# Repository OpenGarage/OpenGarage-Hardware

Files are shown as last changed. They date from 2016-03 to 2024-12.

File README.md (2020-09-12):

OpenGarage is a WiFi universal garage door opener based on the ESP8266 chip.

For details, visit [http://opengarage.io](http://opengarage.io)

This folder contains OpenGarage hardware design files, including:

* Schematic and Board files (EagleCAD)
* BOM, Pin assignments
* Enclosure design files
  - The original 3D design can be found at TinkerCad.com -> search for OpenGarage

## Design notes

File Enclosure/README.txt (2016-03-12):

The 3D printable version is available at:

TinkerCad.com

Search for name 'OpenGarage'.

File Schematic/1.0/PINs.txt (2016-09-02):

ESP8266-WROOM-2 PIN ASSIGNMENTS:

'spare' means the pin is available
for general purpose use and mapped
out on the PCB.

GPIO 0: BUTTON
GPIO 2: LED
GPIO 4: SDA (spare)
GPIO 5: SCL (spare)
GPIO12: SENSOR TRIGGER
GPIO13: BUZZER
GPIO14: SENSOR ECHO
GPIO15: RELAY
GPIO16: RESET (tied to reset to trigger hardware reset)
A0    : ANALOG PIN (spare)

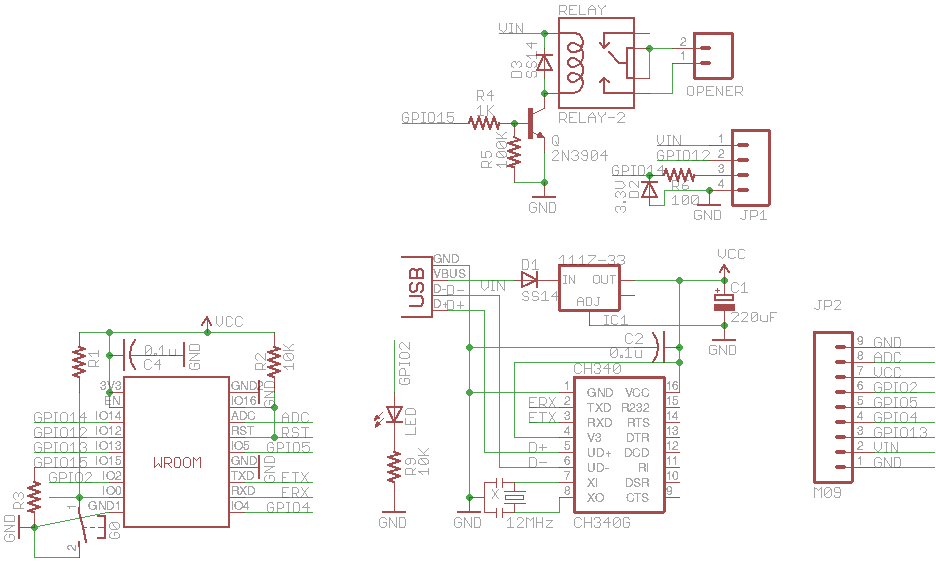
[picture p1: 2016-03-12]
Schematic/1.0/og1.0.png

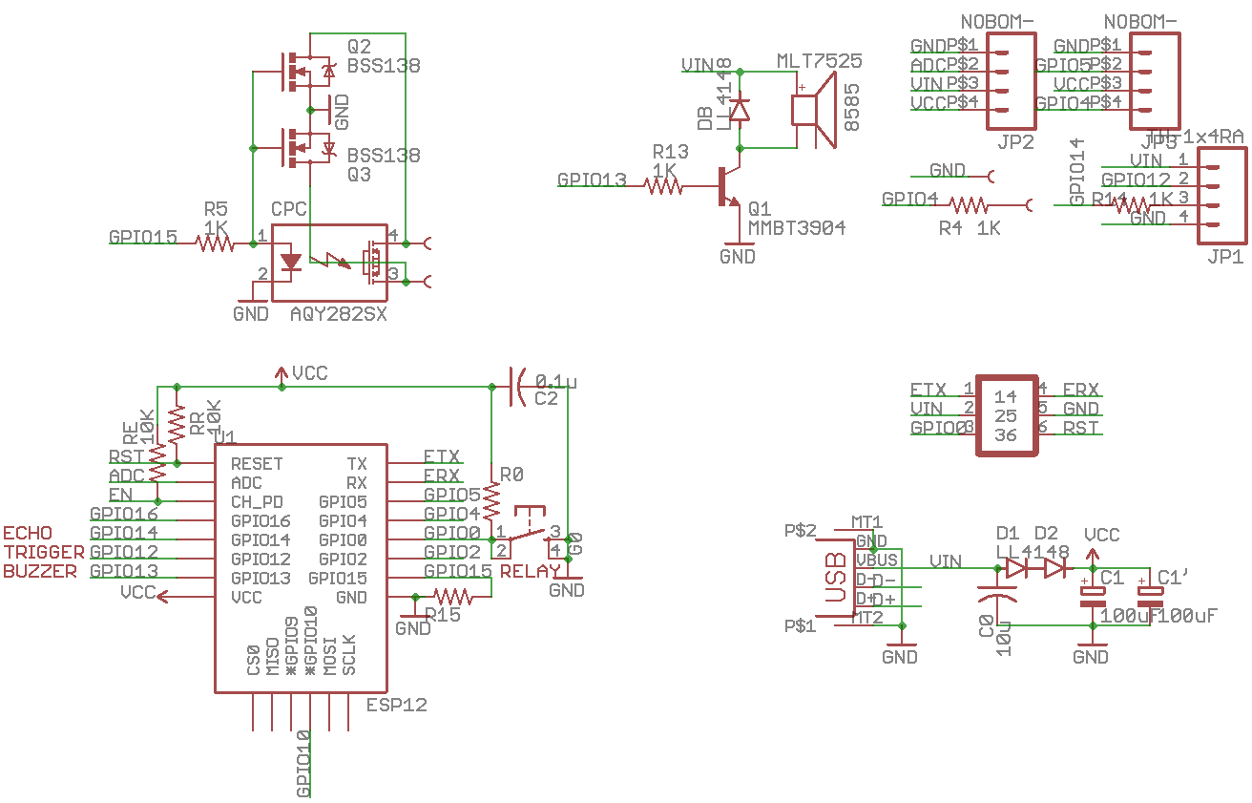
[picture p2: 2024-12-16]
Schematic/2.2/og22_schematic.png

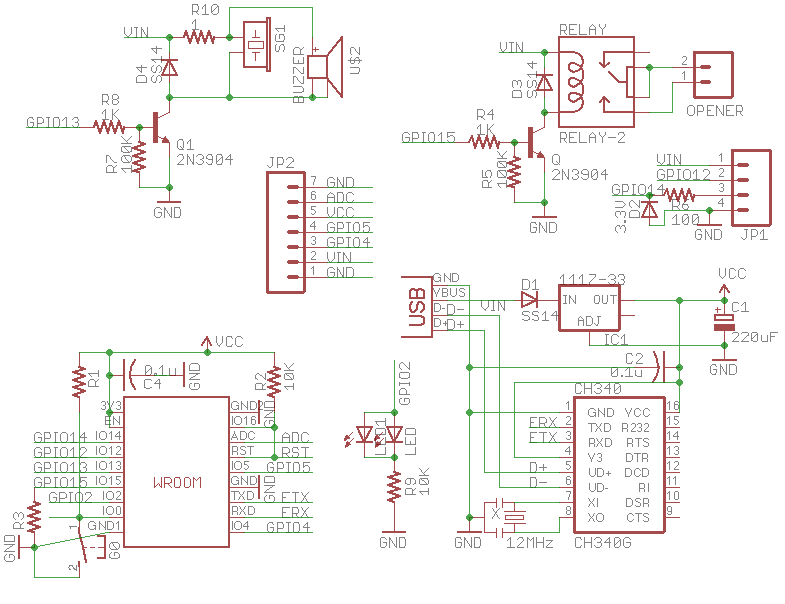
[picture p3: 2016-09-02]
Schematic/1.1/og1.1.png

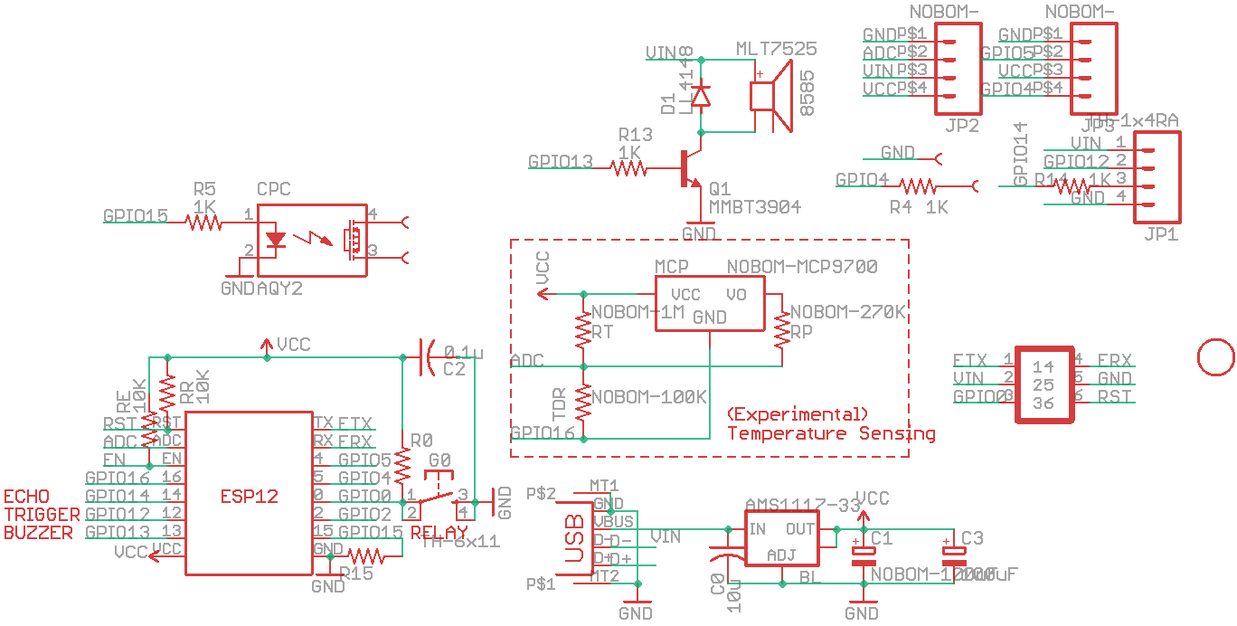
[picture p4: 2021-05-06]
Schematic/2.0/og20_rev2.png

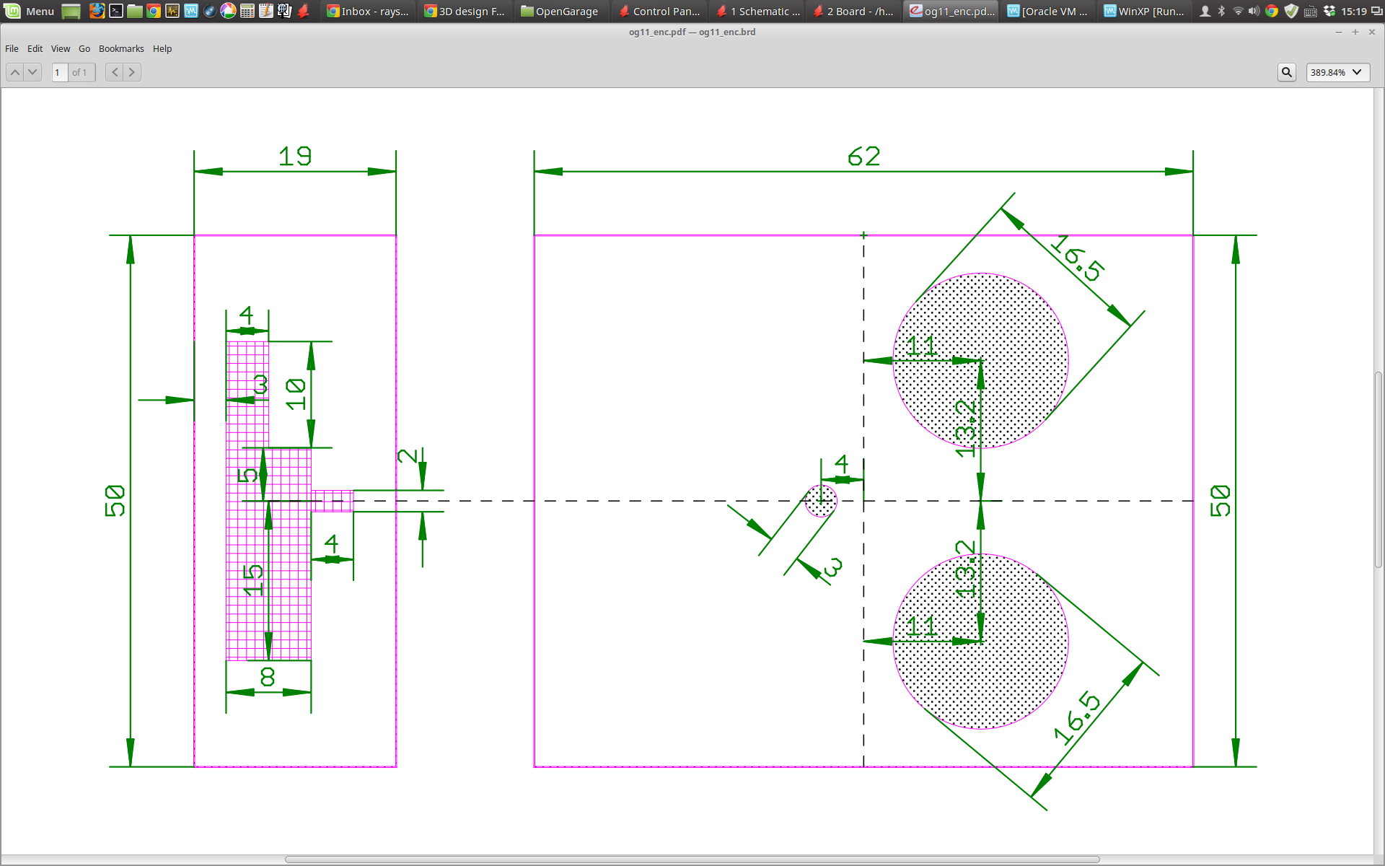
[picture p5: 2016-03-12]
Enclosure/pre-1.4/cutout.png

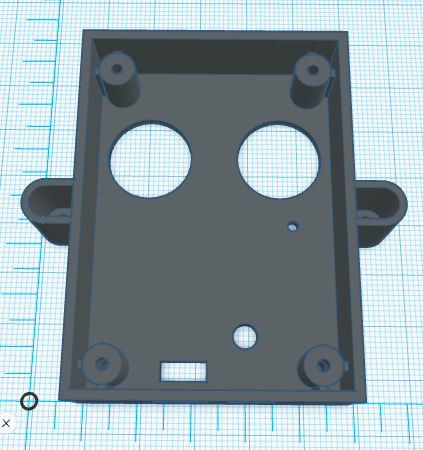
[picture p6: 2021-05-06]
Enclosure/1.4/OG1.4_ENC.png

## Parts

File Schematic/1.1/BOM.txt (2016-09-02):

Part List

Part   Value      Device                Package               Description                          

C1     220uF      CPOL-EUCT3528         CT3528                POLARIZED CAPACITOR, European symbol 
C2     0.1u       C-USC0603K            C0603K                CAPACITOR, American symbol           
C4     0.1u       C-USC0603K            C0603K                CAPACITOR, American symbol           
CH340  CH340G     CH340G                SO16                                                       
D1     SS14       DIODE-DO-214AC        DO-214AC              DIODE                                
D2     3.3V       DIODE-MINIMELF        MINIMELF              DIODE                                
D3     SS14       DIODE-DO-214AC        DO-214AC              DIODE                                
D4     SS14       DIODE-DO-214AC        DO-214AC              DIODE                                
ESP    WROOM02    WROOM02               WROOM                                                      
G0                31-XX                 B3F-31XX              OMRON SWITCH                         
IC1    1117-33    V_REG_LM1117SOT223    SOT223                Voltage Regulator LM1117             
JP1    ULTRASONIC HC-SR04               HC-SR04                          
LED               LEDLED3MM_ABBRV       LED3MM_ABBRV          LED                                  
LED1              LEDCHIPLED_0805       CHIPLED_0805          LED                                  
OPENER OPENER     M024MM-X              SCREWTERMINAL-4MM-2-X Header 2                             
Q      2N3904     TRANSISTOR_NPNSOT23-3 SOT23-3               Transistor NPN                       
Q1     2N3904     TRANSISTOR_NPNSOT23-3 SOT23-3               Transistor NPN                       
R1     10K        R-US_R0603            R0603                 RESISTOR, American symbol            
R2     10K        R-US_R0603            R0603                 RESISTOR, American symbol            
R3     10K        R-US_R0603            R0603                 RESISTOR, American symbol            
R4     1K         R-US_R0603            R0603                 RESISTOR, American symbol            
R5     100K       R-US_R0603            R0603                 RESISTOR, American symbol            
R6     100        R-US_R0603            R0603                 RESISTOR, American symbol            
R7     100K       R-US_R0603            R0603                 RESISTOR, American symbol            
R8     1K         R-US_R0603            R0603                 RESISTOR, American symbol            
R9     10K        R-US_R0603            R0603                 RESISTOR, American symbol            
R10    1          R-US_R0603            R0603                 RESISTOR, American symbol            
RELAY  RELAY-2    HK4100F-5VDC          HK4100F-5VDC                                            
SG1               BUZZERPTH             BUZZER-12MM           Buzzer 12mm                          
U$2    BUZZER     BUZZER                SMT-8585-BUZZER                                            
X      12MHz      RESONATORSMD          RESONATOR-SMD         Resonator                            
X3     USB-MICROB USB-MICROB            USB-MICROB            USB Connectors

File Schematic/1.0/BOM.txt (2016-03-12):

Partlist

Part     Value          Device                Package               

C1       220uF          CPOL-EUCT3528         CT3528                
C2       0.1u           C-USC0603K            C0603K                
C4       0.1u           C-USC0603K            C0603K                
CH340    CH340G         CH340G                SO16                  
D1       SS14           DIODE-DO-214AC        DO-214AC              
D2       3.3V Zener     DIODE-MINIMELF        MINIMELF              
D3       SS14           DIODE-DO-214AC        DO-214AC              
ESP      WROOM02        WROOM02               WROOM                 
G0                      31-XX                 B3F-31XX              
IC1      1117-33        LM1117-ee             SOT223                
JP1      ULTRASONIC     DISTANCE SENSOR       1X04_SONICSENSOR      
LED                     LEDLED3MM_ABBRV       LED3MM_ABBRV          
OPENER   OPENER         M024MM-X              SCREWTERMINAL-4MM-2-X 
Q        2N3904         2N3902                SOT23-3               
R1       10K            R-US_R0603            R0603                 
R2       10K            R-US_R0603            R0603                 
R3       10K            R-US_R0603            R0603                 
R4       1K             R-US_R0603            R0603                 
R5       100K           R-US_R0603            R0603                 
R6       100            R-US_R0603            R0603                 
R9       10K            R-US_R0603            R0603                 
RELAY    RELAY-2        RELAY-2               RELAY-HK4100F-5VDC
X        12MHz          RESONATORSMD          RESONATOR-SMD         
X3       USB-MICROB     USB-MICROB            USB-MICROB

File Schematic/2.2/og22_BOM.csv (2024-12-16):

Name | Designator | Footprint | Quantity
0.1u | C2 | C0603K | 1
1K | R4,R5,R13,R14 | R0603 | 4
10K | R0,R15,RE,RR | R0603 | 4
10u | C0 | C0805K | 1
100uF | C1, C1' | PANASONIC_C | 2
BSS138 | Q2-3 | SOT23-3 | 2
ESP12 | U1 | ESP12E-SMD | 1
LL4148 | D1,D2,DB | MINIMELF | 3
MICROXNJ | X3 | USB-MICROB2 | 1
MLT7525 | 8585 | SMT-8585-BUZZER | 1
MMBT3904 | Q1 | SOT23-3 | 1
TH-1x4RA | JP1 | 1X04_SONICSENSOR_EXT2 | 1
TH-6x11 | G0 | EVQ-Q2 | 1

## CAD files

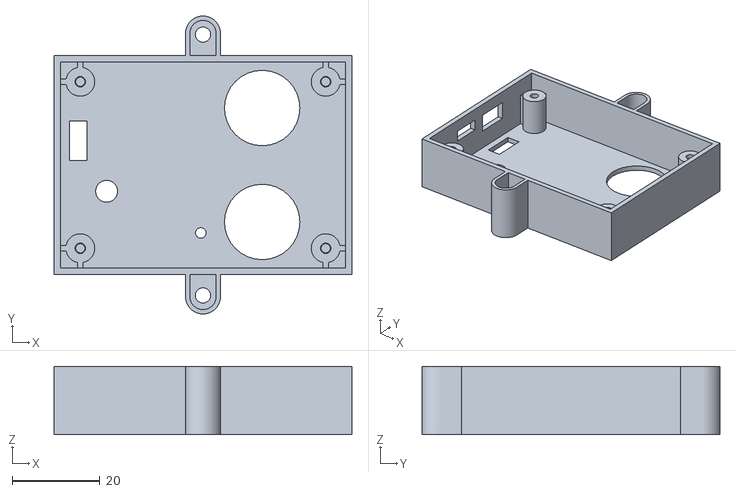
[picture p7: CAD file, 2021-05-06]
Enclosure/1.4/OpenGarage1.4_single.stl
68.0 x 68.0 x 15.6

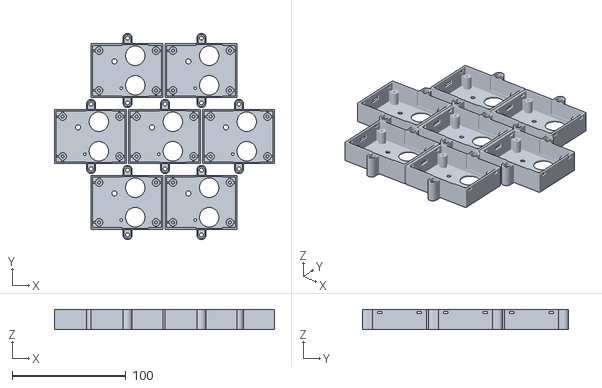
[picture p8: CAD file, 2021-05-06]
Enclosure/2.0/OG2.0ENC.stl
193.4 x 181.4 x 17.6

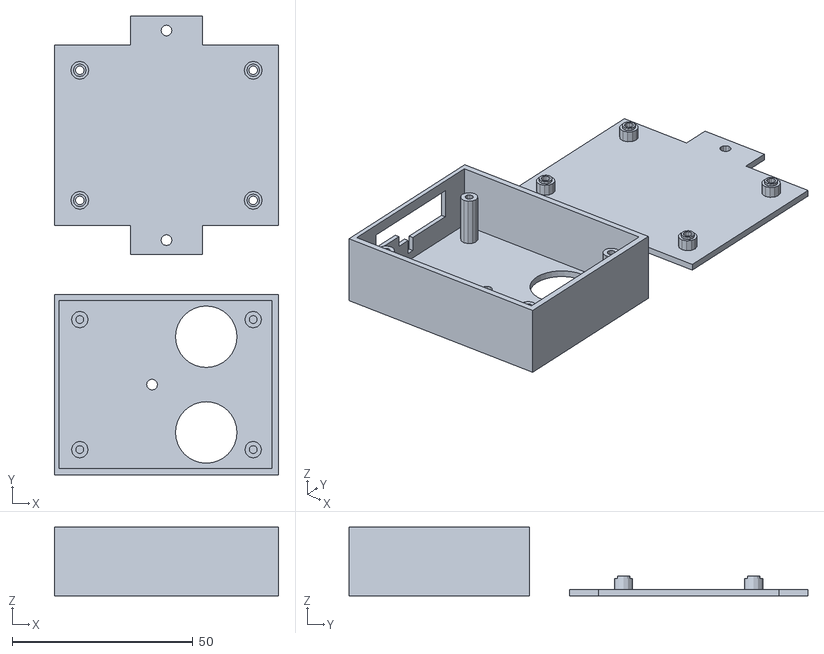
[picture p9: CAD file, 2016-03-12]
Enclosure/pre-1.4/enclosure_3d.obj
62.0 x 127.0 x 19.0

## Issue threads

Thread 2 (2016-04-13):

Value of R9

terrag42, 2016-04-13:
I noticed that in your schematic and in the BOM, R9 is specified as 10k Ohms. If I'm using a normal LED whose rated voltage is about 3.2V, I don't think it will be very bright, is this what you have found? Since the LED's voltage is coming from the ESP8266 (3.3 V), would it be OK for me to change the value of R9 to something like 220 ohms or even 47 ohms?

rayshobby, 2016-04-20:
Sorry, that's a typo. It should be something small (like 220ohm or 330ohm).

Closed 2016-04-20.

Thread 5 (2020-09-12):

Version 1.4 Open Source Hardware Version?

wiesl, 2020-09-12:
Hello,

Ordered 2x OpenGarage Hardware. Unfortunately this is Version V1.4 of OpenGarage Hardware.

Where can I find V1.4 of the Schematic and PCB Eagle files?

Thnx.

rayshobby, 2020-09-12:
I've just checked it in.

wiesl, 2020-09-13:
Thnx.

Closed 2020-09-12.

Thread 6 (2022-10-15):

What type is C3 on the 2.0 Hardware

Dreamoffice, 2022-10-15:
Hello

what type is the condensator C3?

rayshobby, 2022-10-24:
The BOM has each component's type and value:
https://github.com/OpenGarage/OpenGarage-Hardware/blob/master/Schematic/2.0/og20_rev2_BOM.csv

Closed 2022-10-24.

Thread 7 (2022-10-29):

missing part? buzzer not working

Dreamoffice, 2022-10-29:
Hello. i just assembled one Opengarage 2.0 but the buzzer is not working. how can i trouble shoot? this is my board. did i missed some parts except the ultra sonic sensor?

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

rayshobby, 2022-10-31:
Q1 (MMBT3904) on your board is missing.

Closed 2022-10-31.

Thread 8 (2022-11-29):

Feature request: control garage lights

danepowell, 2022-11-29:
Most garage doors include 120 V lights on the power head that automatically turn on when the garage opens, and can also be controlled by a switch on the opener.

It would be awesome to control these lights with OpenGarage. I'm guessing this would require a second relay, since the light button has its own control wire (green for old Genie models like mine).

rayshobby, 2022-11-29:
I've looked at this a while back. This highly depends on the garage door system. I have a LiftMaster (non-security+ 2.0), and I noticed its door button has a light control switch. It uses the same two wires for door control and light control. I took apart the door button panel, and found that the door control simply shorts the two wires (as expected), and the light control connects a 1uF capacitor across the two wires. Some online posts also documented this feature:
https://forum.arduino.cc/t/using-esp8266-arduino-and-2n2222-for-garage-door/472101
I've actually made a variant of OpenGarage that uses two solid state relays, the first one simply shorts the two wires, and the second one has a 1uF capacitor in series. This allows for controlling both the door and the light.

However, if a garage door system uses security+ 2.0, then it's a completely different story -- it uses rolling code so is not as simple as connecting a 1uF capacitor across the two wires. I am sure other brands would use yet different ways for light control. So I concluded it would be hard to design one circuit that handles all these different ways for light control.

danepowell, 2022-11-30:
Makes sense, thanks a lot for the context. I wonder if you could leave some open slots on the board for folks to insert their own relays or caps or daughter board to accommodate whatever system. Maybe that's overkill :shrug:

Closed 2023-11-16.

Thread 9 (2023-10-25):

Possible to use with LA400 Gate Opener?

TopBanana123, 2023-10-25:
I'm wondering if its possible to connect this up to an LA400 gate opener? Its a fairly recent model and also apparently has single button control on the circuit board

rayshobby, 2023-11-16:
If directly wiring OpenGarage to your door's button terminals doesn't work, then as long as you have a working button/remote, you can always solder two wires to the button/remote, and wire them to OpenGarage. That should always work.

Closed 2023-11-16.

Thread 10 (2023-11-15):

Enclosure not found on TinkerFiles

TopBanana123, 2023-11-15:
I have an issue with the OpenGarage enclosure in that it does not accept a standard USB cable because the USB Port is too recessed

I made the hole bigger and in the process cracked the case, and would like to print another. The GitHub page does to search for OpenGarage on TinkerHub, however I get no results

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

Is there an STL file I could get to print another?

HoECoder, 2023-11-16:
I found them here:
https://www.tinkercad.com/things/fSLeOxNVjwK-opengarage-enclosure

And here:
https://www.tinkercad.com/things/2qRHEHzTHSL-opengarage-enclosure-v2

Depending on your HW Version

rayshobby, 2023-11-16:
The 3D model in STL format is available in the Enclosure folder:
https://github.com/OpenGarage/OpenGarage-Hardware/tree/master/Enclosure

TopBanana123, 2023-11-16:
Perfect, thanks guys! Would be nice if the main page linked to the STL instead of asking you to search

Closed 2023-11-16.

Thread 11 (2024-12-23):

SSR dead for the second time

tofuSCHNITZEL, 2024-12-23:
Hi,
I have an OG Rev 2.0 and I just had to swap the SSR for the second time in around a year because it was completely fried and did not switch anymore...
maybe this is caused by the particular garagemotor I have but I was just wondering if you have some experience with dying solid state relays on the opengarage board...?

cheers

rayshobby, 2025-01-25:
This is likely due to your garage door system is presenting a high voltage to OpenGarage. The SSR can tolerate up to 60V. I've seen very occasionally some garage door systems that present 110V, which will definitely fry the SSR. Have you measured the voltage on the two wires of your garage door system? Almost all modern systems use 12VDC, which is well below the limit. If this continues to be a problem, you may want to use an electromechanical relay which can tolerate up to 220V.

tofuSCHNITZEL, 2025-01-25:
I admit I have not yet measured the "switching" wires because I assumed that they come pot-free from the garage motor pcb... but probably not ;) I have wired a "real" relay to the opengarage pcb and I don't expect any issues anymore ;) thanks!

Closed 2025-01-25.

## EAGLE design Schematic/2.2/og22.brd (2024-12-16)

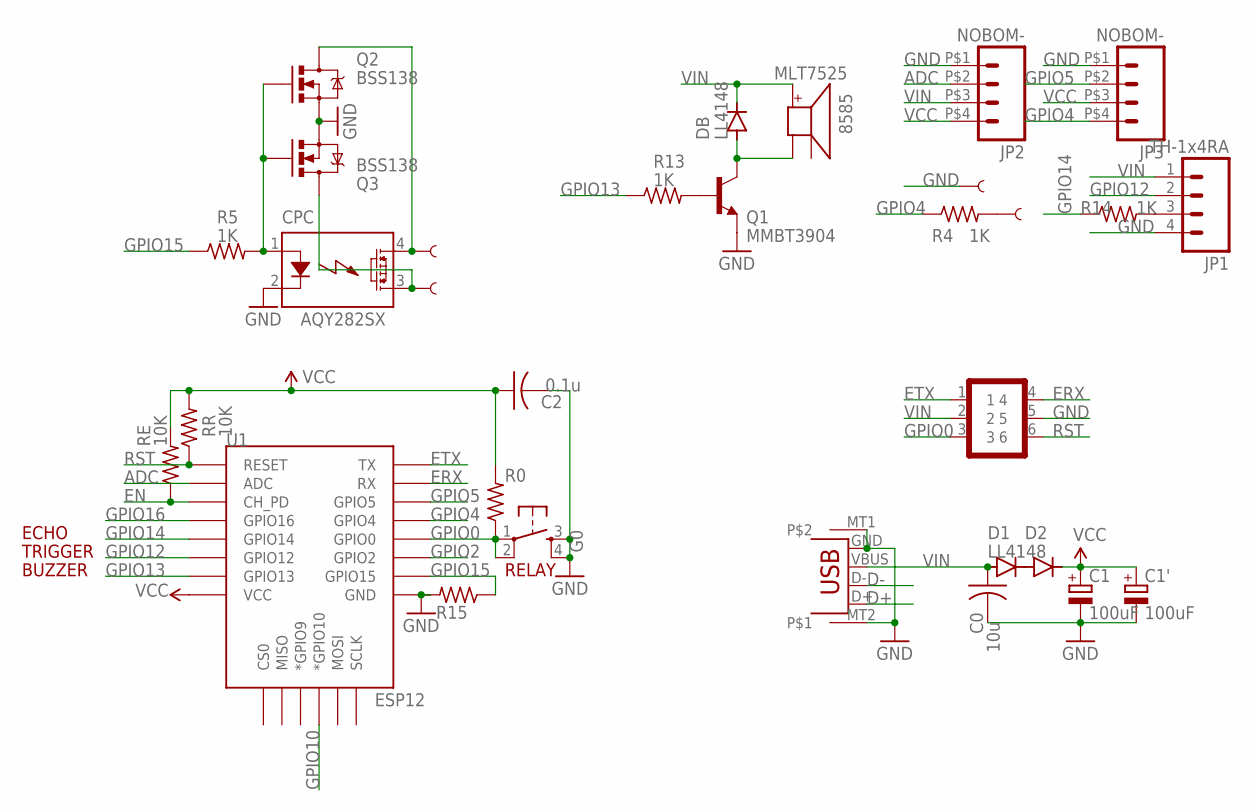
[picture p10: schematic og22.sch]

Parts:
8585: MLT7525; SMT-8585-BUZZER
C0: 10u; C0805K
C1, C1': 100uF; PANASONIC_C
C2: 0.1u; C0603K
CPC: AQY282SX; PHOTOMOS
D1, D2: LL4148; MINIMELF
DB: LL4148; MINIMELF
G0: TH-6x11; EVQ-Q2
JP1: TH-1x4RA; 1X04_SONICSENSOR_EXT2
JP2, JP3: NOBOM-; 1X04-2X2
Q1: MMBT3904; SOT23-3
Q2, Q3: BSS138; SOT23-3
R0, R15: 10K; R0603
R4, R5, R13, R14: 1K; R0603
RE: 10K; R0603
RR: 10K; R0603
U1: ESP12; ESP12E-SMD
U$1: NOBOM-GF2x3; GOLDFINGER_2X3
U$2, U$3, U$4, U$5: NOBOM-; PETAL-7MM-DOUBLE
X3: MICROXNJ; USB-MICROB2

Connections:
ADC: JP2.P$2 (2), U1.ADC
D+: X3.D+
D-: X3.D-
EN: RE.1, U1.CH_PD
ERX: U1.RXD0 (RX), U$1.4
ETX: U1.TXD0 (TX), U$1.1
GND: C0.2, C1.-, C1'.-, C2.2, CPC.2 (K), G0.3, G0.4, JP1.4, JP2.P$1 (1), JP3.P$1 (1), Q1.2 (E), Q2.2 (S), Q3.2 (S), R15.2, U1.GND, U$1.5, U$4.P$1, X3.GND, X3.MT1, X3.MT2
GPIO0: G0.1, G0.2, R0.1, U1.GPIO0, U$1.3
GPIO2: U1.GPIO2
GPIO4: JP3.P$4 (4), R4.1, U1.GPIO4
GPIO5: JP3.P$2 (2), U1.GPIO5
GPIO10: U1.GPIO10 (*GPIO10)
GPIO12: JP1.2, U1.GPIO12
GPIO13: R13.1, U1.GPIO13
GPIO14: R14.1, U1.GPIO14
GPIO15: R5.1, R15.1, U1.GPIO15
GPIO16: U1.GPIO16
unnamed: CPC.4 (DS1), Q2.3 (D), U$3.P$1
unnamed: CPC.3 (DS2), Q3.3 (D), U$2.P$1
unnamed: R4.2, U$5.P$1
unnamed: JP1.3, R14.2
unnamed: 8585.-, DB.A, Q1.3 (C)
unnamed: Q1.1 (B), R13.2
unnamed: CPC.1 (A), Q2.1 (G), Q3.1 (G), R5.2
unnamed: D1.C, D2.A
RST: RR.1, U1.RESET, U$1.6
VCC: C1.+, C1'.+, C2.1, D2.C, JP2.P$4 (4), JP3.P$3 (3), R0.2, RE.2, RR.2, U1.VCC
VIN: 8585.+, C0.1, D1.A, DB.C, JP1.1, JP2.P$3 (3), U$1.2, X3.VBUS

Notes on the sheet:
RELAY
BUZZER
ECHO
TRIGGER

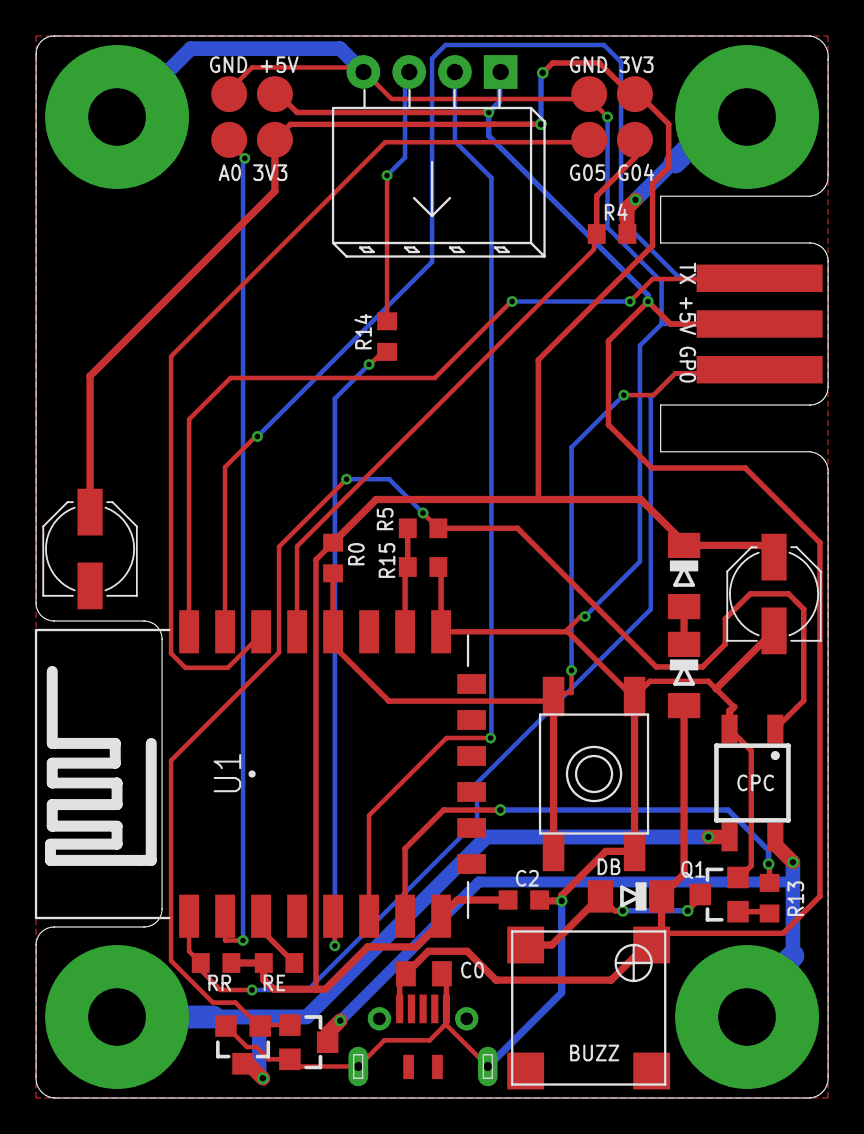
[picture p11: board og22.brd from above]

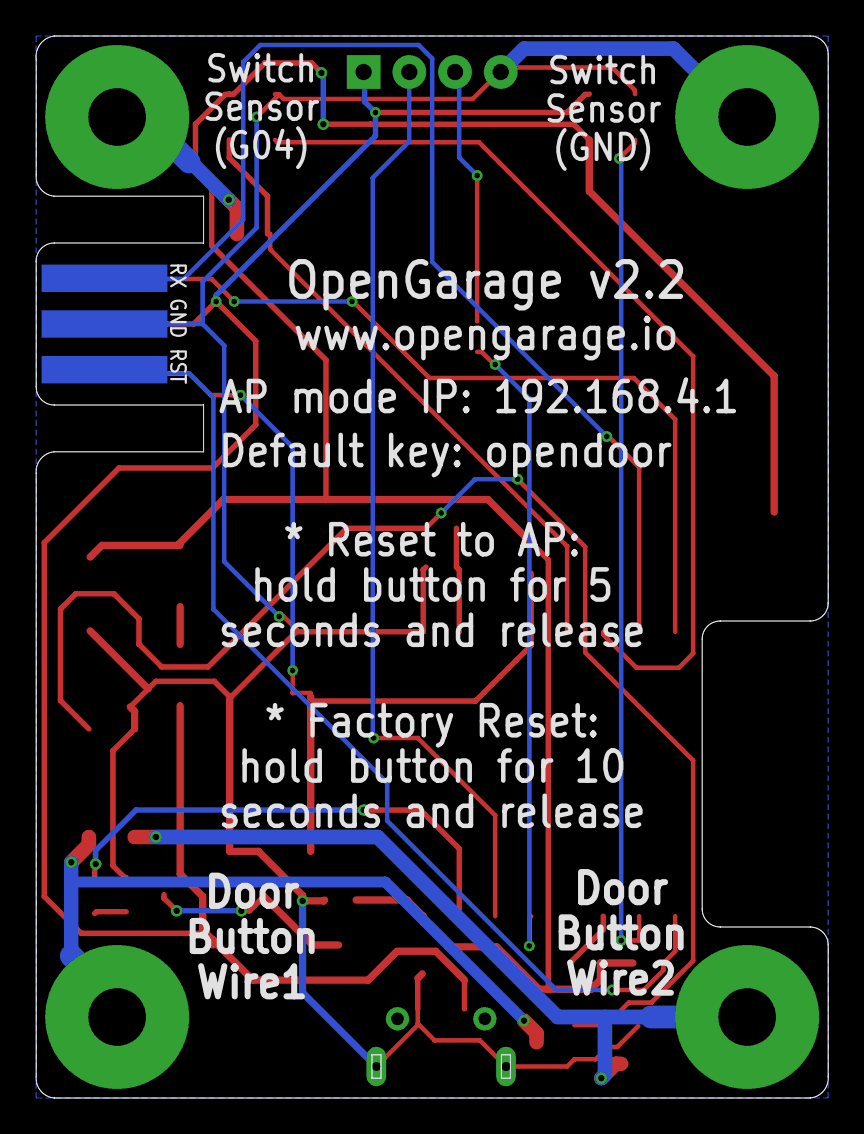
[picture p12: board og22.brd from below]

Board: 2 copper layers, 44.0 x 59.0 mm, 31 parts (4 on the bottom side), 23 nets.

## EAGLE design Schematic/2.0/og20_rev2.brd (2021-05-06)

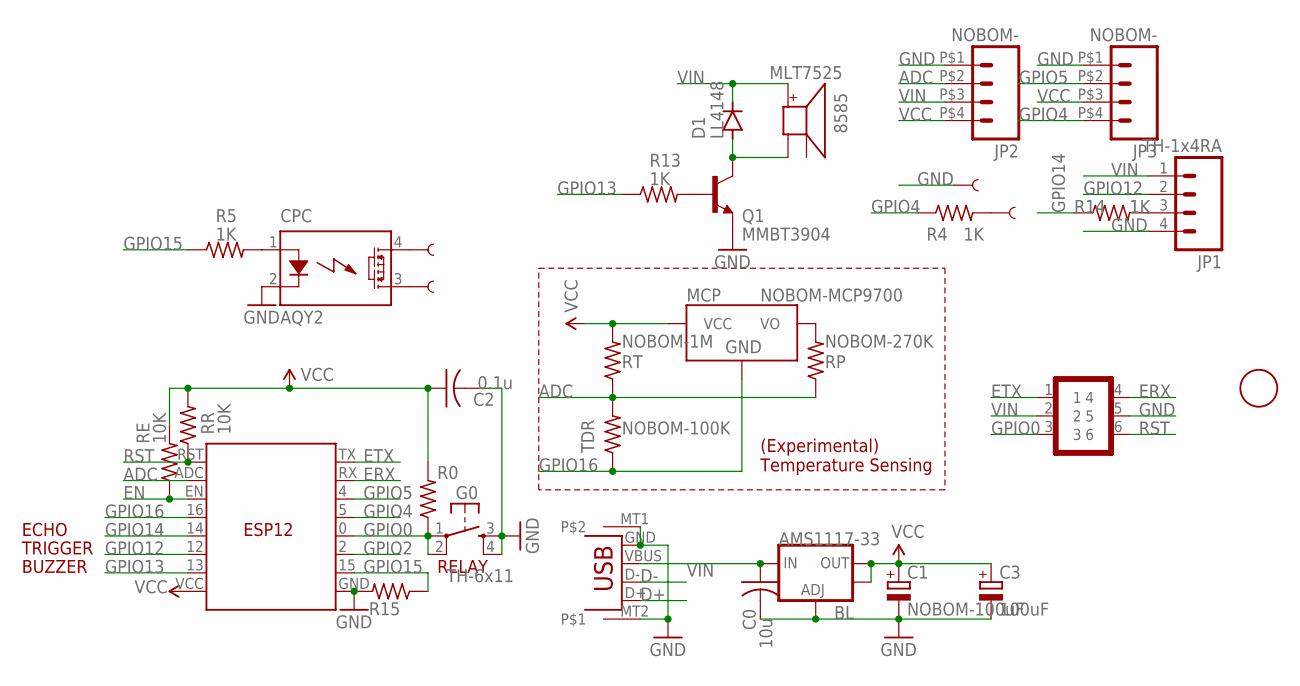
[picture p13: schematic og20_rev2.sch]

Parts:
0F: FIDUCIAL; FIDUCIAL_1MM
8585: MLT7525; SMT-8585-BUZZER
BL: AMS1117-33; SOT223
C0: 10u; C0805K
C1: NOBOM-100uF; B/3528-21R
C2: 0.1u; C0603K
C3: 100uF; PANASONIC_C
CPC: AQY2; PHOTOMOS
D1: LL4148; MINIMELF
ESP: ESP8266; ESP12
G0: TH-6x11; TACTILE-PTH
JP1: TH-1x4RA; 1X04_SONICSENSOR_EXT2
JP2, JP3: NOBOM-; 1X04-2X2
MCP: NOBOM-MCP9700; SOT23-3
Q1: MMBT3904; SOT23-3
R0, R15: 10K; R0603
R4, R5, R13, R14: 1K; R0603
RE: 10K; R0603
RP: NOBOM-270K; R0603
RR: 10K; R0603
RT: NOBOM-1M; R0603
TDR: NOBOM-100K; R0805
U$1: NOBOM-GF2x3; GOLDFINGER_2X3
U$2, U$3, U$4, U$5: NOBOM-; PETAL-3MM-1SIDE
X3: MICROXNJ; USB-MICROB2

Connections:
ADC: ESP.ADC, JP2.P$2 (2), RP.1, RT.1, TDR.2
D+: X3.D+
D-: X3.D-
EN: ESP.EN, RE.1
ERX: ESP.RX, U$1.4
ETX: ESP.TX, U$1.1
GND: BL.1 (ADJ), C0.2, C1.-, C2.2, C3.-, CPC.2 (K), ESP.GND, G0.3, G0.4, JP1.4, JP2.P$1 (1), JP3.P$1 (1), Q1.2 (E), R15.2, U$1.5, U$4.P$1, X3.GND, X3.MT1, X3.MT2
GPIO0: ESP.0 (G0), G0.1, G0.2, R0.1, U$1.3
GPIO2: ESP.2 (G2)
GPIO4: ESP.5 (G5), JP3.P$4 (4), R4.1
GPIO5: ESP.4 (G4), JP3.P$2 (2)
GPIO12: ESP.12 (G12), JP1.2
GPIO13: ESP.13 (G13), R13.1
GPIO14: ESP.14 (G14), R14.1
GPIO15: ESP.15 (G15), R5.1, R15.1
GPIO16: ESP.16 (G16), MCP.3 (GND), TDR.1
unnamed: CPC.4 (DS1), U$2.P$1
unnamed: CPC.3 (DS2), U$3.P$1
unnamed: R4.2, U$5.P$1
unnamed: JP1.3, R14.2
unnamed: 8585.-, D1.A, Q1.3 (C)
unnamed: MCP.2 (VO), RP.2
unnamed: Q1.1 (B), R13.2
unnamed: CPC.1 (A), R5.2
RST: ESP.RST, RR.1, U$1.6
VCC: BL.2 (OUT), BL.4 (OUT), C1.+, C2.1, C3.+, ESP.VCC, JP2.P$4 (4), JP3.P$3 (3), MCP.1 (VCC), R0.2, RE.2, RR.2, RT.2
VIN: 8585.+, BL.3 (IN), C0.1, D1.C, JP1.1, JP2.P$3 (3), U$1.2, X3.VBUS

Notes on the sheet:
RELAY
BUZZER
ECHO
TRIGGER
(Experimental) Temperature Sensing

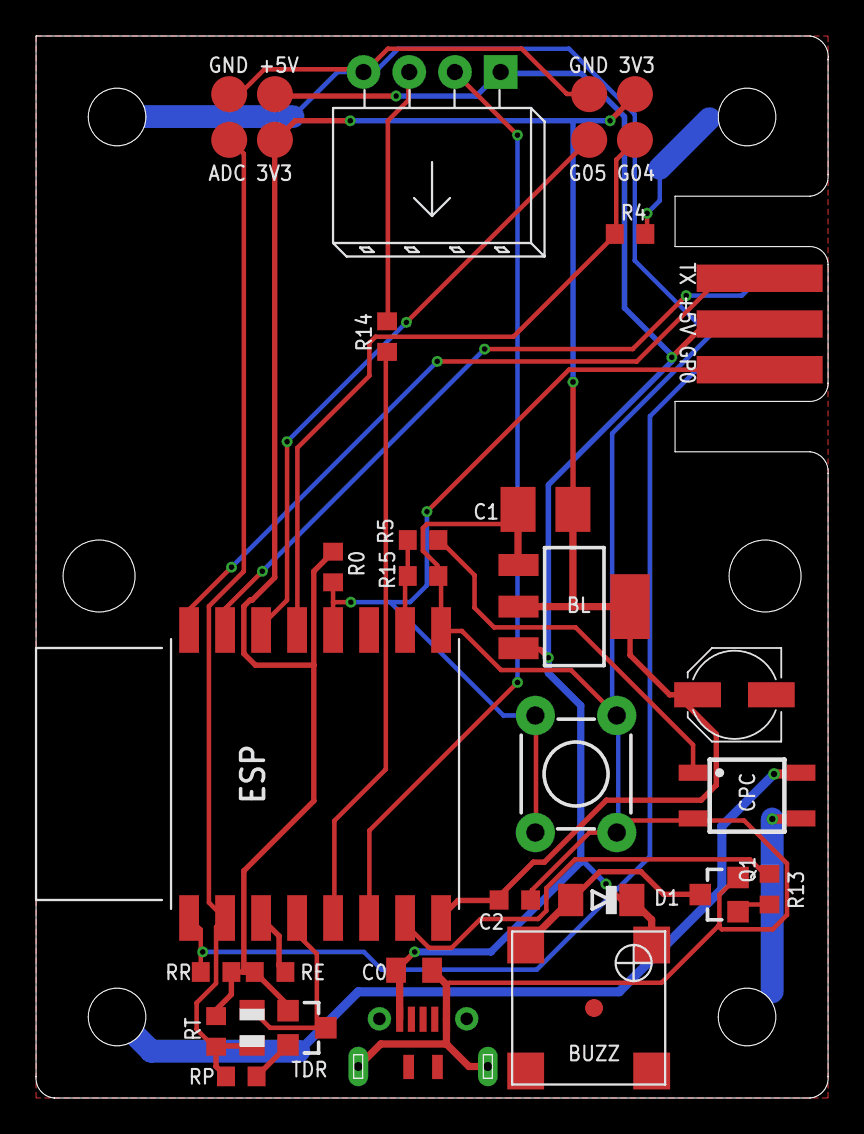
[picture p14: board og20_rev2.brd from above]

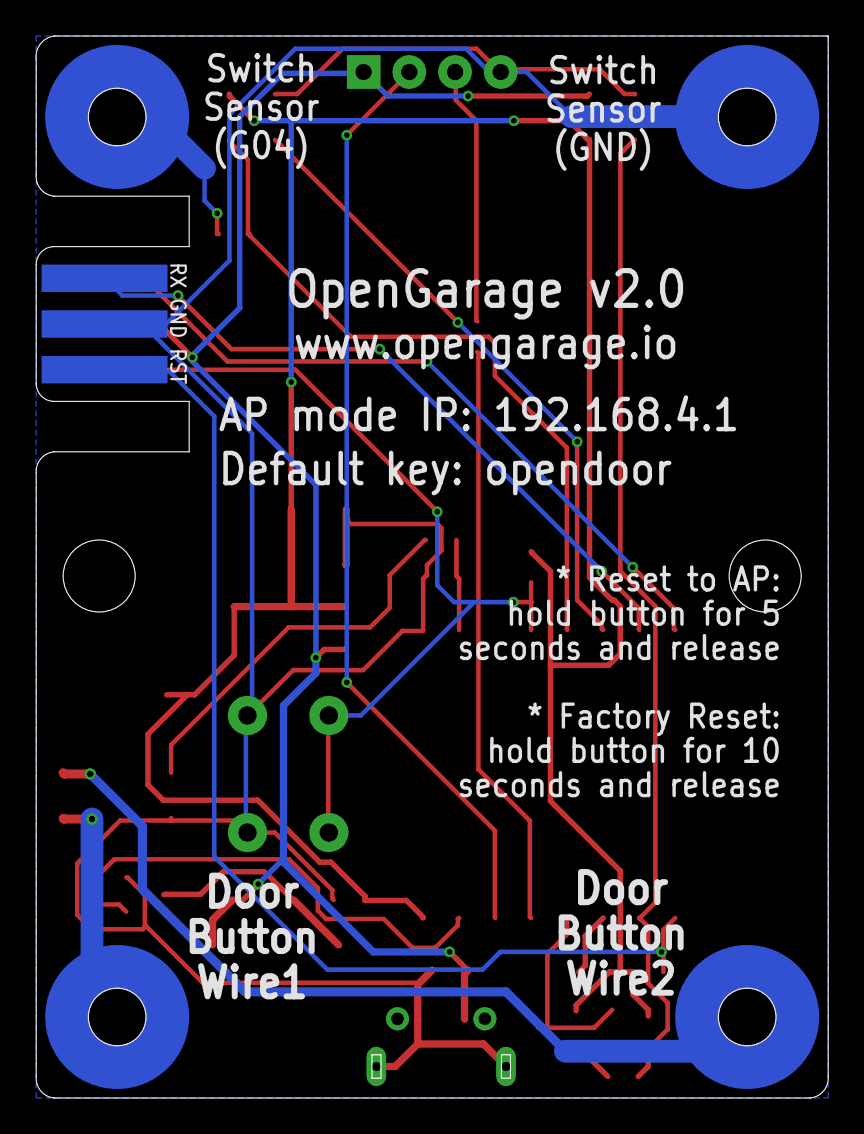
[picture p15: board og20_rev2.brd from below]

Board: 2 copper layers, 44.0 x 59.0 mm, 33 parts (4 on the bottom side), 24 nets.

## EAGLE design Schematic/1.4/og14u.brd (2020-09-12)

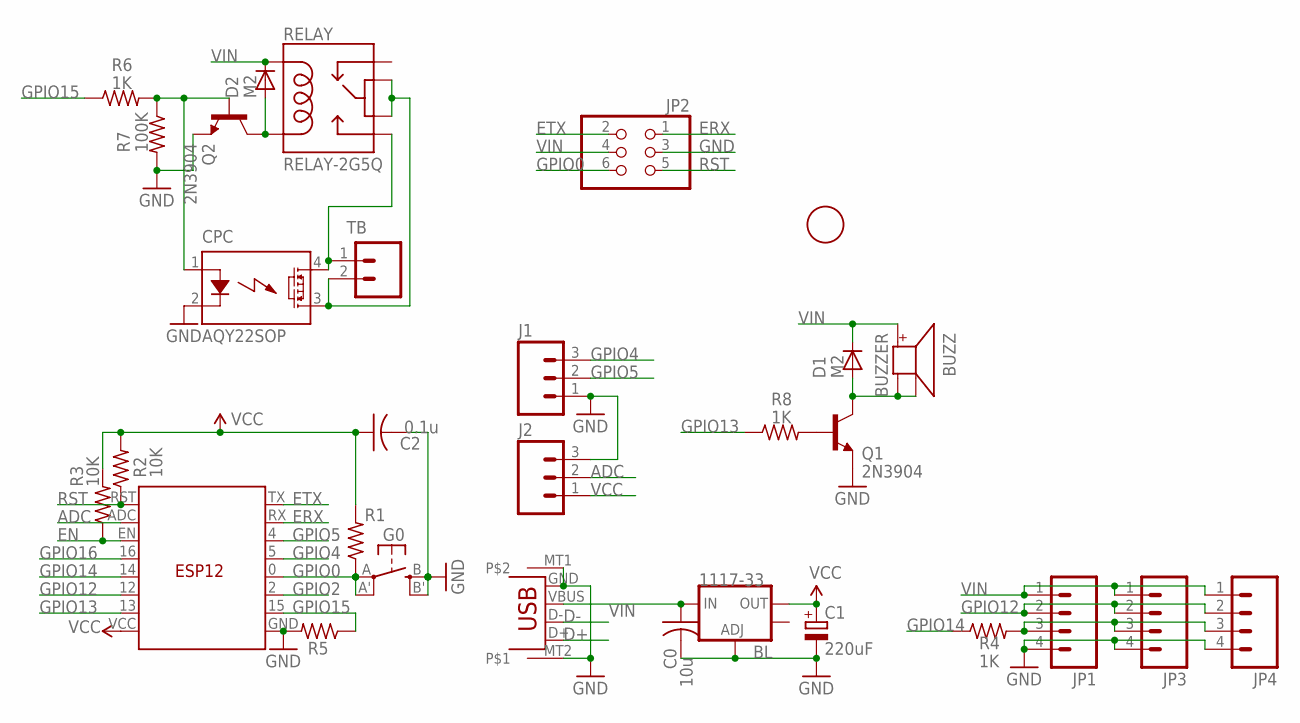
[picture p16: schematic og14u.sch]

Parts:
1F: FIDUCIAL; FIDUCIAL_1MM
BL: 1117-33; SOT223
BUZZ: BUZZER; SMT-8585-BUZZER
C0: 10u; C0805K
C1: 220uF; B/3528-21R
C2: 0.1u; C0603K
CPC: AQY22SOP; SOP04
D1, D2: M2; DO-214AC
ESP: ESP12
G0: SPST_TACT-EVQQ2; EVQ-Q2
J1, J2: M03PTH; 1X03
JP1: M04SONICSMD; 1X04_SONICSENSOR_SMD
JP2: PINHD-2X3; 2X03
JP3, JP4: M04DIST; 1X04_NO_SILK_DIST
Q1, Q2: 2N3904; SOT23-3
R1, R2, R3, R5: 10K; R0603
R4, R6, R8: 1K; R0603
R7: 100K; R0603
RELAY: RELAY-2G5Q; RELAY-G5V
TB: OPENER; SCREWTERMINAL-5MM-2-KF
X3: USB+GND; USB-MICROB2

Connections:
ADC: ESP.ADC, J2.2
D+: X3.D+
D-: X3.D-
EN: ESP.EN, R3.1
ERX: ESP.RX, JP2.1
ETX: ESP.TX, JP2.2
GND: BL.1 (ADJ), C0.2, C1.-, C2.2, CPC.2 (K), ESP.GND, G0.B (S), G0.B' (S1), J1.1, J2.3, JP1.4, JP2.3, JP3.4, JP4.4, Q1.2 (E), Q2.2 (E), R5.2, R7.2, X3.GND, X3.MT1, X3.MT2
GPIO0: ESP.0 (G0), G0.A, G0.A' (P1), JP2.6, R1.1
GPIO2: ESP.2 (G2)
GPIO4: ESP.5 (G5), J1.3
GPIO5: ESP.4 (G4), J1.2
GPIO12: ESP.12 (G12), JP1.2, JP3.2, JP4.2
GPIO13: ESP.13 (G13), R8.1
GPIO14: ESP.14 (G14), R4.1
GPIO15: ESP.15 (G15), R5.1, R6.1
GPIO16: ESP.16 (G16)
unnamed: CPC.4 (DS1), RELAY.10, TB.1
unnamed: CPC.3 (DS2), RELAY.5, RELAY.6, TB.2
unnamed: JP1.3, JP3.3, JP4.3, R4.2
unnamed: BUZZ.-, BUZZ.A-, D1.A, Q1.3 (C)
unnamed: Q1.1 (B), R8.2
unnamed: D2.A, Q2.3 (C), RELAY.9
unnamed: CPC.1 (A), Q2.1 (B), R6.2, R7.1
RST: ESP.RST, JP2.5, R2.1
VCC: BL.2 (OUT), C1.+, C2.1, ESP.VCC, J2.1, R1.2, R2.2, R3.2
VIN: BL.3 (IN), BUZZ.+, C0.1, D1.C, D2.C, JP1.1, JP2.4, JP3.1, JP4.1, RELAY.2, X3.VBUS

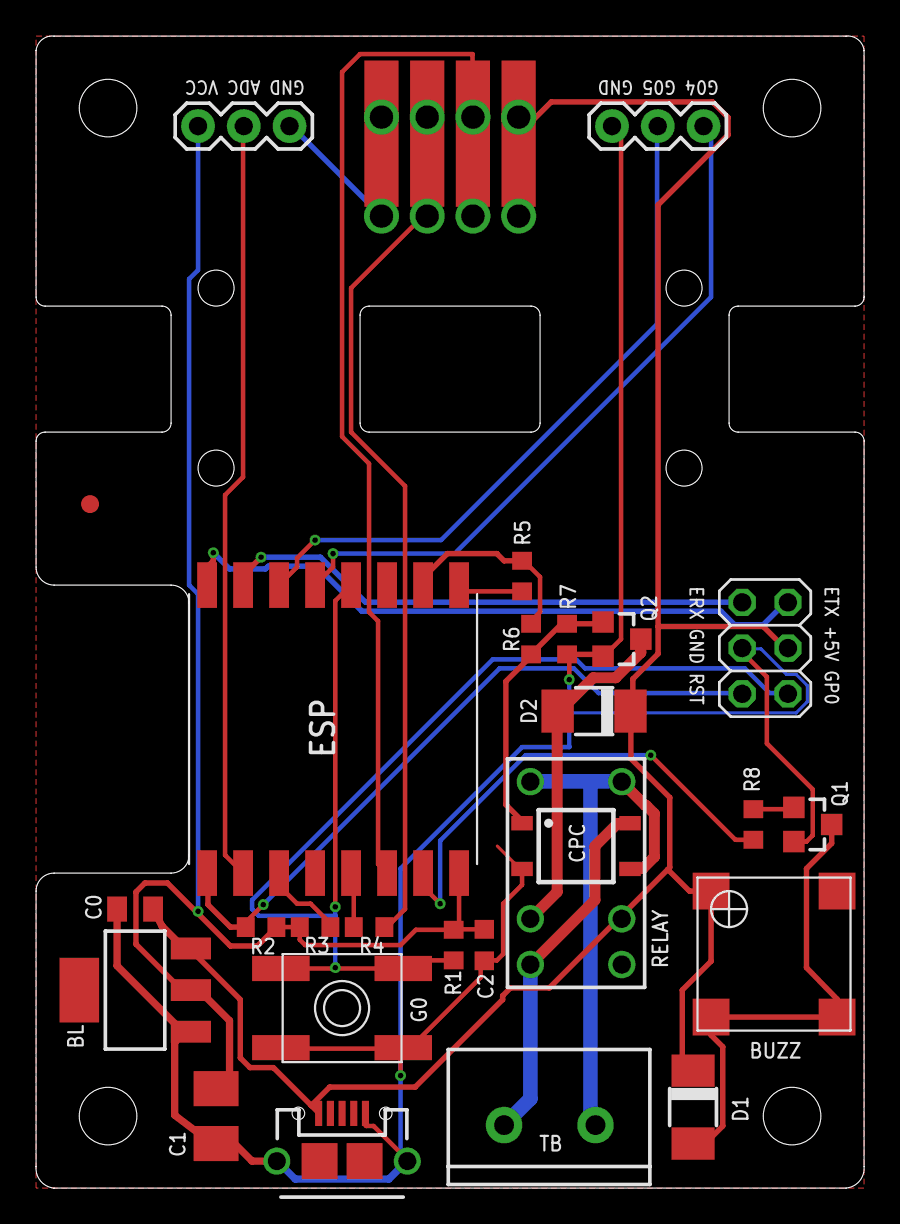
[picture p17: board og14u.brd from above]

Board: 2 copper layers, 46.0 x 64.0 mm, 30 parts (0 on the bottom side), 22 nets.

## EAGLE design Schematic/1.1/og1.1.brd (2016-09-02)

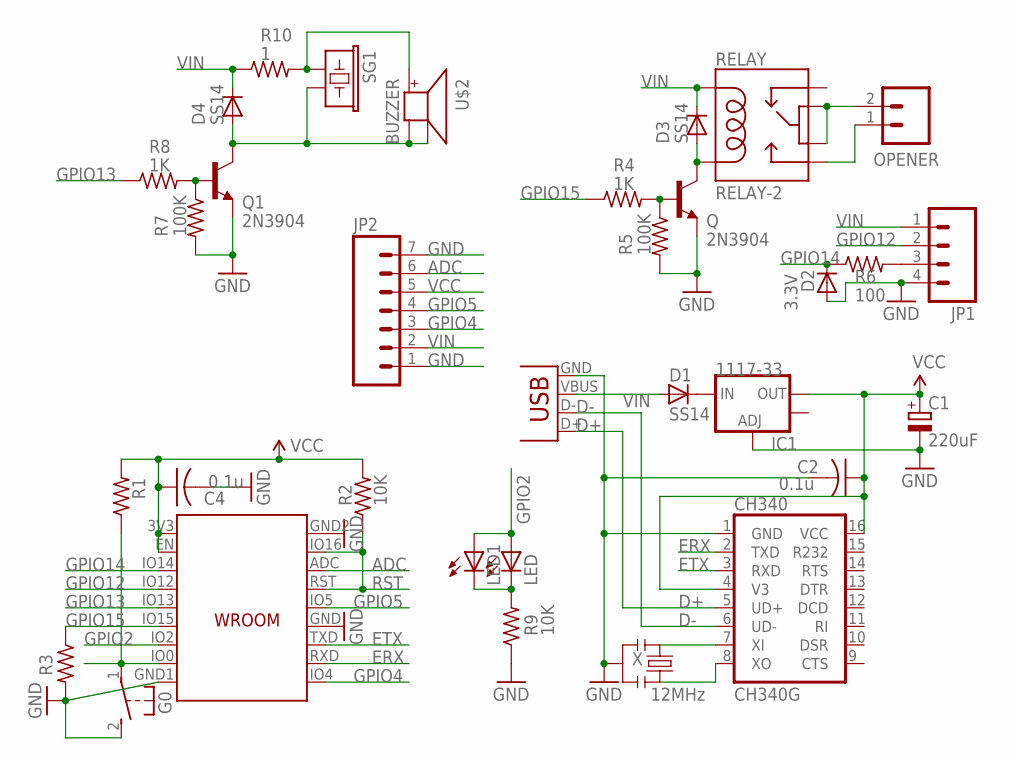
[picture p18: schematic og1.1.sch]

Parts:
C1: 220uF; CT3528
C2, C4: 0.1u; C0603K
CH340: CH340G; SO16
D1, D3, D4: SS14; DO-214AC
D2: 3.3V; MINIMELF
ESP: WROOM02; WROOM
G0: 31-XX; B3F-31XX
IC1: 1117-33; SOT223
JP1: M04SONIC; 1X04_SONICSENSOR
JP2: M07; 1X07
LED: LEDLED3MM_ABBRV; LED3MM_ABBRV
LED1: LEDCHIPLED_0805; CHIPLED_0805
OPENER: OPENER; SCREWTERMINAL-4MM-2-X
Q, Q1: 2N3904; SOT23-3
R1, R2, R3, R9: 10K; R0603
R4, R8: 1K; R0603
R5, R7: 100K; R0603
R6: 100; R0603
R10: 1; R0603
RELAY: RELAY-2; RELAY-HK4100F
SG1: BUZZERPTH; BUZZER-12MM
U$2: BUZZER; SMT-8585-BUZZER
X: 12MHz; RESONATOR-SMD
X3: USB-MICROB

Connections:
ADC: ESP.ADC, JP2.6
D+: CH340.5 (UD+), X3.D+
D-: CH340.6 (UD-), X3.D-
ERX: CH340.2 (TXD), ESP.RXD (RX)
ETX: CH340.3 (RXD), ESP.TXD (TX)
GND: C1.-, C2.2, C4.2, CH340.1 (GND), D2.A, ESP.GND, ESP.GND1, ESP.GND2, G0.2 (S), IC1.1 (ADJ), JP1.4, JP2.1, JP2.7, Q.2 (E), Q1.2 (E), R3.2, R5.2, R7.2, R9.1, X.2, X3.GND
GPIO0: ESP.IO0, G0.1, R1.1
GPIO2: ESP.IO2, LED.A, LED1.A
GPIO4: ESP.IO4, JP2.3
GPIO5: ESP.IO5, JP2.4
GPIO12: ESP.IO12, JP1.2
GPIO13: ESP.IO13, R8.1
GPIO14: D2.C, ESP.IO14, R6.1
GPIO15: ESP.IO15, R3.1, R4.1
unnamed: D1.C, IC1.3 (IN)
unnamed: Q.1 (B), R4.2, R5.1
unnamed: OPENER.2, RELAY.5, RELAY.6
unnamed: OPENER.1, RELAY.10
unnamed: JP1.3, R6.2
unnamed: D4.A, Q1.3 (C), SG1.- (2), U$2.-, U$2.A-
unnamed: LED.K (C), LED1.C, R9.2
unnamed: Q1.1 (B), R7.1, R8.2
unnamed: R10.2, SG1.+ (1), U$2.+
unnamed: CH340.7 (XI), X.1
unnamed: CH340.8 (XO), X.3
unnamed: D3.A, Q.3 (C), RELAY.9
RST: ESP.IO16, ESP.RST, R2.1
VCC: C1.+, C2.1, C4.1, CH340.4 (V3), CH340.16 (VCC), ESP.3V3 (VCC), ESP.EN, IC1.2 (OUT), JP2.5, R1.2, R2.2
VIN: D1.A, D3.C, D4.C, JP1.1, JP2.2, R10.1, RELAY.2, X3.VBUS

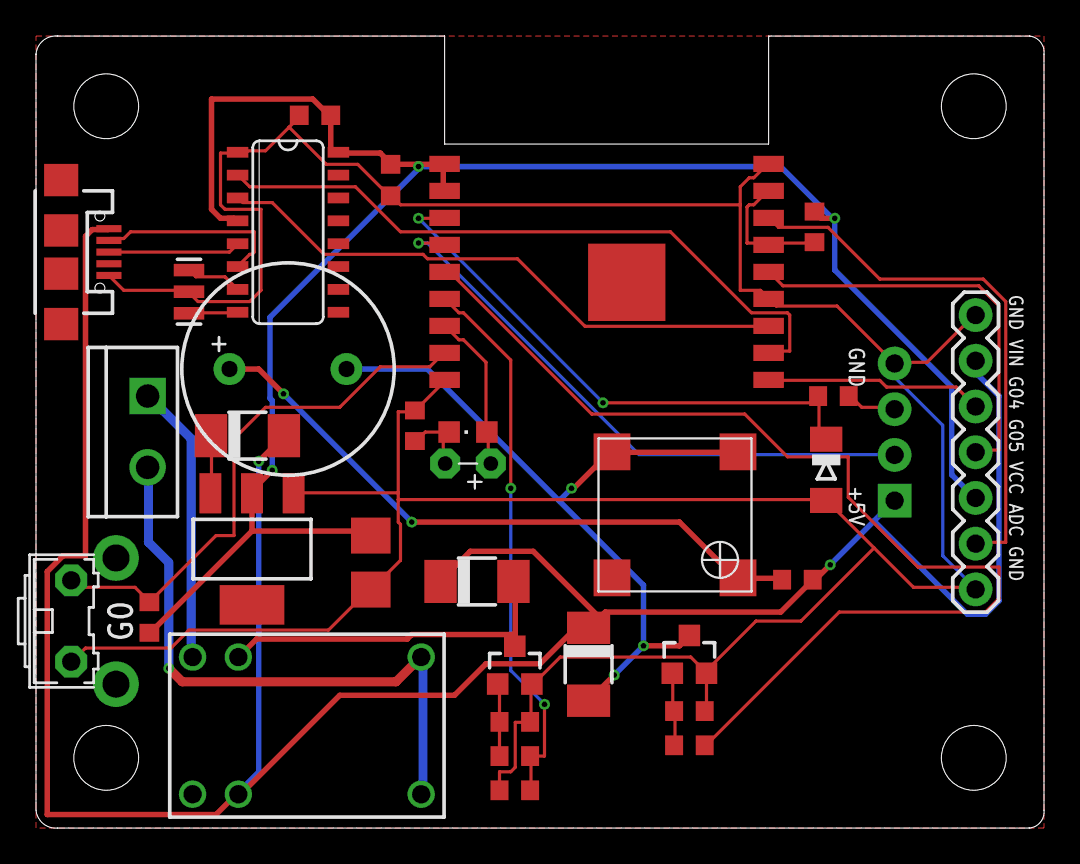
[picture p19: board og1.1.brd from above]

Board: 2 copper layers, 56.0 x 44.0 mm, 33 parts (0 on the bottom side), 29 nets.

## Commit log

2016-03-12 check in schematic and enclosure design files
    [enclosure_3d.obj, og1.0.brd, og1.0.sch]
2016-09-02 check in updated schematic
    [og1.1.brd, og1.1.sch]
2016-10-01 update pin definitions
2020-09-12 add version 1.4 Eagle files
    [og14u.brd, og14u.sch]
2021-05-06 add OG 2.0 schematic, bom, and enclosure design
    [OG2.0ENC.stl, OpenGarage1.4_single.stl, og20_rev2.brd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]
2021-05-06 re-structure enclosure folder
    [OpenGarage1.4_single.stl, enclosure_3d.obj]
2024-12-16 add version 2.2 hardware design files
    [og22.brd, og22.sch, og22_BOM.csv]

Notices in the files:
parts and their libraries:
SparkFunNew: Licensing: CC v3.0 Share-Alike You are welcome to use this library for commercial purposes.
